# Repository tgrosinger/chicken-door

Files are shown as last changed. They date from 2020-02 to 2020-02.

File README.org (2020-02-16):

* Automated Chicken Door

This repo contains the plans I used to create an automated chicken coop door. I
do not think it was much cheaper than buying one off the shelf, and it took way,
way longer to build. But I learned so much about circuitry components and
design, Arduino programming, and using a laser cutter to build the mounts. I
hope you too can benefit from following the process detailed in this repository
to build your own custom solution.

** Design
This opener is designed to be used with a light (1/8" acrylic) door, captured in
table saw kerf rails on either side. The door slides up and down by being raised
with the stepper motor, or let out by the motor. When the door is fully opened
or closed, a solenoid is used to latch the door in place and the motor is
powered down.

** Future Improvements
The biggest improvement this door needs right now is waterproofing. The motor
and switches are exposed to the elements, sheltered only by the roof overhang. I
am sure that they will not last very long in the rainy PNW climate here. In
version 2 I will look into sourcing water resistant components or building
housings as necessary.

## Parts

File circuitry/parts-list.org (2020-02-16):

* Circuitry Parts List
All of these parts were ordered from Adafruit. While not the cheapest, Adafruit
provides a valuable service to beginners by narrowing down the nearly infinite
field of components into a few of each category to choose from.

** Arduino
- [[https://www.adafruit.com/product/3677][ItsyBitsy 32u4 - 5v]]
** Motors and Solenoid
- [[https://www.adafruit.com/product/324][NEMA-17 Stepper motor - 12v 350mA]]
- [[https://www.adafruit.com/product/412][Small Push-Pull Solenoid - 12v]]
- 2x [[https://www.adafruit.com/product/807][Dual H-Bridge - L293D]]
  + I have learned since ordering this that it is a pretty inefficient chip, but
    it seems to be working just fine for my needs.
** Control
- [[https://www.adafruit.com/product/1384][Log-scale Analog Light Sensor]]
- 2x [[https://www.adafruit.com/product/819][Micro Switch w/ Roller Lever]]
** Connectivity
- 3x [[https://www.adafruit.com/product/2880][2-pin JST Plug + Receptacle Set]]
  + Open limit switch
  + Close limit switch
  + Solenoid
- [[https://www.adafruit.com/product/1663][3-pin JST Plug + Receptacle Set]]
  + For connecting two toggle switches for manual override
  + Optionally add one additional if you want the light sensor detached from the
    board
- [[https://www.adafruit.com/product/578][4-pin JST Plug + Receptacle Set]]
  + For connecting the stepper motor
- [[https://www.adafruit.com/product/373][2.1mm DC barrel jack]]
- [[https://www.adafruit.com/product/2670][Bakelite Perfboard Plates]]
** Also need
- 12v power supply
  + This could be a wall outlet, or a car battery
- Breadboard and jumper cables for prototyping
- Acrylic or light plywood for the door
- Acrylic for the light sensor window

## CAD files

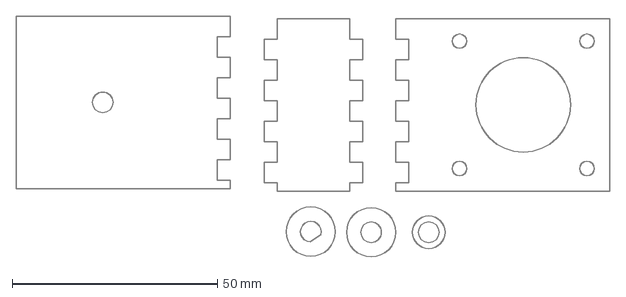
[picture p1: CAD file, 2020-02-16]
motor-mount/MotorMount.dxf
144.3 x 58.6 mm

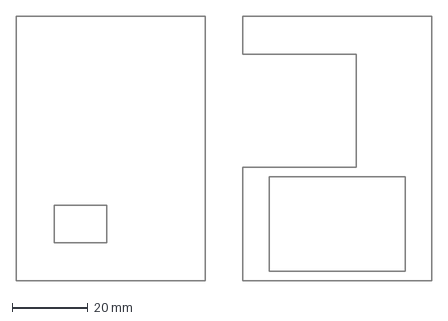
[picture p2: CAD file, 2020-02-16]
motor-mount/v2/BoardMount.dxf
110.0 x 70.0 mm

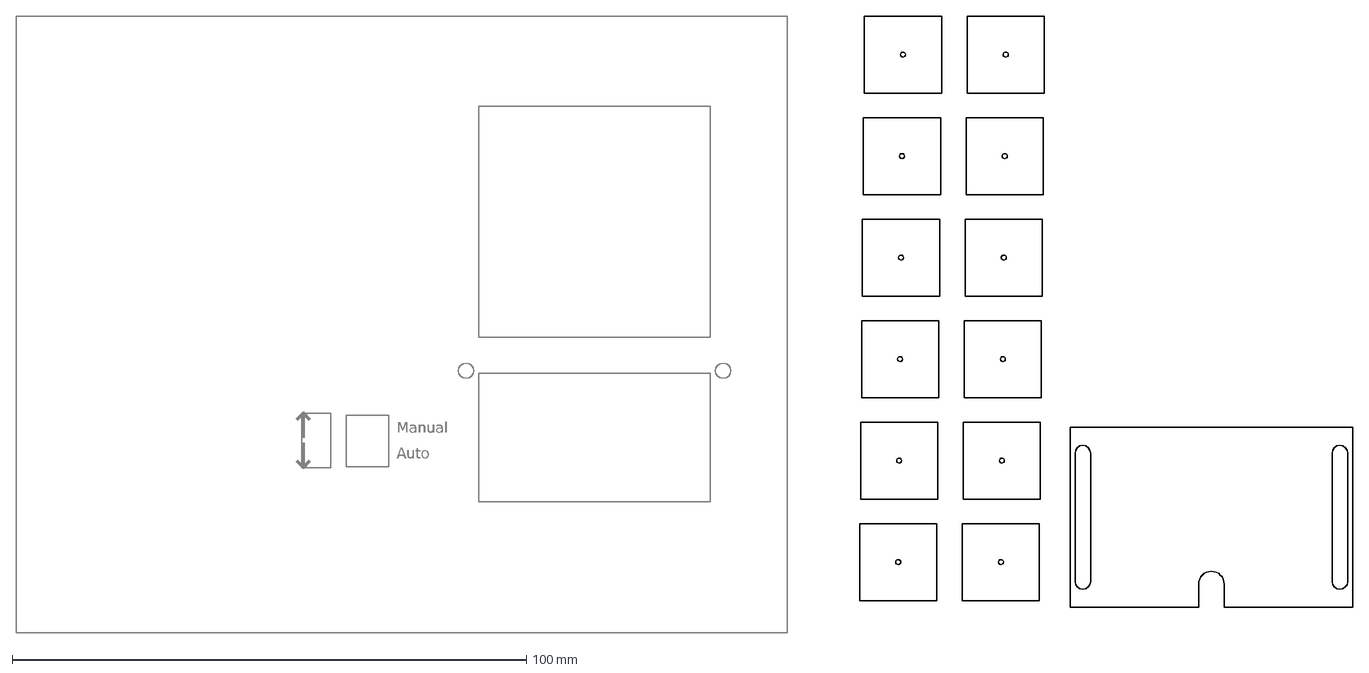
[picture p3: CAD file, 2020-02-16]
motor-mount/BoardMount.dxf
Auto
Manual
↑
↓

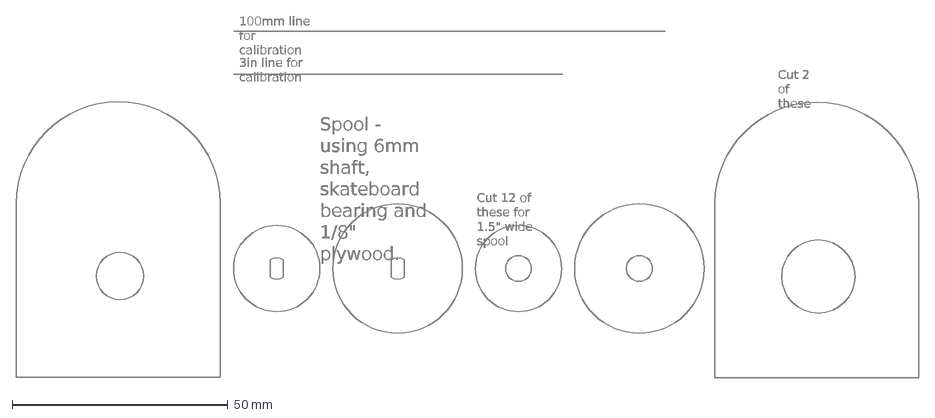
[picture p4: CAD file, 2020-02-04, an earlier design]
motor-mount/v1/chicken-door.dxf
Spool - using 6mm shaft, skateboard bearing and 1/8" plywood.
Cut 12 of these for 1.5" wide spool
Cut 2 of these
100mm line for calibration
3in line for calibration

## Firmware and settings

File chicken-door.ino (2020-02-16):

#include <Stepper.h>

// LED Values
const int ledPin = 13;

// Stepper Values
const int stepsPerRevolution = 200;
const int coilA1Pin = 12;
const int coilA2Pin = 11;
const int coilB1Pin = 10;
const int coilB2Pin = 9;
const int driverEnPin = 0;
Stepper doorStepper = Stepper(stepsPerRevolution, coilA1Pin, coilA2Pin, coilB1Pin, coilB2Pin);

// Solenoid Values
const int solPin = 1;
const int solCoilA1Pin = 7;
const int solCoilA2Pin = 5;

// Light Meter Values
const int lightPin = A5;
const int doorOpenThreshold = 220;
const int doorCloseThreshold = 200;
const long doorCloseDelay = 20 * 1000L; // 20 seconds

int lightValue = 0;

// Switches
const int doorCloseSwitch = A1;
const int doorOpenSwitch = A2;
const int manualSwitch = A3;
const int openCloseSwitch = A4;

// Door States
const int doorOpen = 1;
const int doorClosed = 2;
const int doorPreClose = 3;
const int doorUnknown = 4;
const int doorJammed = 5; // took too long to gravity close
const int doorJamCleared = 6;
const int expectedDoorCloseDurationMilli = 16 * 1000L; // 16 seconds
const unsigned long minDoorOpenDuration = 8 * 60 * 60 * 1000L; // 8 hours

const bool debug = true;
const int sec = 1000;

void engageSolenoid() {
  digitalWrite(solPin, LOW);
  digitalWrite(solCoilA1Pin, LOW);
  digitalWrite(solCoilA2Pin, LOW);
  delay(sec/2);
}

void disengageSolenoid() {
  digitalWrite(solPin, HIGH);
  digitalWrite(solCoilA1Pin, HIGH);
  digitalWrite(solCoilA2Pin, LOW);
  delay(sec/2);
}

class Door {
  int doorState;
  unsigned long doorPreCloseMillis;
  unsigned long doorLastOpenMillis;

  public:
  Door() {
    doorState = doorUnknown;
    doorPreCloseMillis = 0;
    doorLastOpenMillis = 0;
  }

  void Update() {
    int lightValue = analogRead(lightPin);
    if (debug) {
      Serial.print("Light level: ");
      Serial.println(lightValue);
    }

    if (doorState == doorJammed || doorState == doorUnknown) {
      Open();
    }

    
    if (digitalRead(manualSwitch) == LOW) {
      if (digitalRead(openCloseSwitch) == LOW) {
        Serial.println("door manually set to open");
        Open();
      } else {
        Serial.println("door manually set to close");
        Close();
      }

      return;
    }

    if (lightValue > doorOpenThreshold) {
      Open();
    } else if (lightValue < doorCloseThreshold) {
      CloseWithPreCloseChecks();
    }
  }

  void Open() {
    if (doorState == doorOpen && digitalRead(doorOpenSwitch) == LOW) {
      return;
    }
 
    Serial.println("Going to open the door");
    
    digitalWrite(driverEnPin, HIGH); // Enable the motor
    disengageSolenoid(); // Retract the lock

    while(digitalRead(doorOpenSwitch) == HIGH) {
      doorStepper.step(stepsPerRevolution / 8); // Open the door, 1/8 rotation
    }
 
    engageSolenoid(); // Extend the lock
    doorStepper.step(-1 * stepsPerRevolution / 4); // Lower door onto solenoid
    digitalWrite(driverEnPin, LOW); // Disable the motor

    Serial.println("Door is open");

    if (doorState == doorJammed) {
      doorState = doorJamCleared;
    } else {
      doorState = doorOpen;
      doorLastOpenMillis = millis(); 
    }
  }

  void CloseWithPreCloseChecks() {
    if (doorState == doorClosed && digitalRead(doorCloseSwitch) == LOW) {
      return;
    }

    if ((unsigned long)(millis() - doorLastOpenMillis) < minDoorOpenDuration) {
      Serial.println("Not closing, opened too recently");
      delay(sec);
      return;
    }

    if (doorState == doorOpen || doorState == doorJamCleared) {
      Serial.println("Entering door pre-close");
      doorState = doorPreClose;
      doorPreCloseMillis = millis();
    }

    if (doorState == doorPreClose) {
      long elapsed = ((unsigned long)(millis() - doorPreCloseMillis));
      if (elapsed < doorCloseDelay) {
        delay(sec);
        return;
      }

      // Finished pre-close delay
    }

    Close();
  }

  void Close() {
    if (doorState == doorClosed && digitalRead(doorCloseSwitch) == LOW) {
      return;
    }

    Serial.println("Going to close the door");

    digitalWrite(driverEnPin, HIGH); // Enable the motor
    doorStepper.step(stepsPerRevolution / 3); // Lift door off solenoid
    disengageSolenoid(); // Retract the lock

    unsigned long doorCloseStart = millis();
    unsigned long interval = expectedDoorCloseDurationMilli * 1.5;
    while(digitalRead(doorCloseSwitch) == HIGH &&
            (unsigned long)(millis() - doorCloseStart) < interval) {
      doorStepper.step(stepsPerRevolution / 8 * -1); // Close the door, 1/8 rotation
    }
    doorStepper.step(stepsPerRevolution / 8 * -1);

    if (digitalRead(doorCloseSwitch) == HIGH) {
      Serial.println("Door did not close, likely jammed");
      doorState = doorJammed;
      // Do not diable the solenoid or motor jump to update loop to bounce open and closed
      return;
    }

    Serial.print("Door close took ");
    Serial.print(millis() - doorCloseStart);
    Serial.println(" millis");
 
    engageSolenoid(); // Extend the lock
    digitalWrite(driverEnPin, LOW); // Disable the motor

    Serial.println("Door is closed");
    doorState = doorClosed;
  }
};

class Flasher {
  int ledPin;      // the number of the LED pin
  long OnTime;     // milliseconds of on-time
  long OffTime;    // milliseconds of off-time

  int ledState;                   // ledState used to set the LED
  unsigned long previousMillis;   // will store last time LED was updated

  public:
  Flasher(int pin, long on, long off) {
    ledPin = pin;
    pinMode(ledPin, OUTPUT);     
 
    OnTime = on;
    OffTime = off;

    ledState = LOW; 
    previousMillis = 0;
  }
 
  void Update() {
    // check to see if it's time to change the state of the LED
    unsigned long currentMillis = millis();
 
    if((ledState == HIGH) && ((unsigned long)(currentMillis - previousMillis) >= OnTime)) {
      ledState = LOW;  // Turn it off
      previousMillis = currentMillis;  // Remember the time
      digitalWrite(ledPin, ledState);  // Update the actual LED
    } else if ((ledState == LOW) && ((unsigned long)(currentMillis - previousMillis) >= OffTime)) {
      ledState = HIGH;  // turn it on
      previousMillis = currentMillis;   // Remember the time
      digitalWrite(ledPin, ledState);   // Update the actual LED
    }
  }
};

// the setup function runs once when you press reset or power the board
void setup() {
  pinMode(ledPin, OUTPUT);

  // initialize stepper pins
  pinMode(coilA1Pin, OUTPUT);
  pinMode(coilA2Pin, OUTPUT);
  pinMode(coilB1Pin, OUTPUT);
  pinMode(coilB2Pin, OUTPUT);
  doorStepper.setSpeed(40);

  // initialize pins
  pinMode(solPin, OUTPUT);
  pinMode(solCoilA1Pin, OUTPUT);
  pinMode(solCoilA2Pin, OUTPUT);
  pinMode(driverEnPin, OUTPUT);
  pinMode(doorOpenSwitch,  INPUT_PULLUP);
  pinMode(doorCloseSwitch, INPUT_PULLUP);
  pinMode(manualSwitch, INPUT_PULLUP);
  pinMode(openCloseSwitch, INPUT_PULLUP);

  //Initiate Serial communication
  if (debug) {
    Serial.begin(9600);
  }

  delay(2000);
}

Flasher led = Flasher(ledPin, 500, 500);
Door door = Door();

// loop runs forever
void loop() {
  led.Update();
  door.Update();
  
  delay(500);
}

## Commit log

2020-02-04 Version 1
    Unfortunately this version was not powerful enough. It used a uni-polar
    geared down motor which was not capable of lifting the door.
    [ChickenDoor.fzz, chicken-door.dxf]
2020-02-16 Version 2
    [BoardMount.dxf, ChickenDoor.fzz, MotorMount.dxf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]
